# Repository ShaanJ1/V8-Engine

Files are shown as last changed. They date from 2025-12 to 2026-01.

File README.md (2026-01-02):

# V8 Engine
A working 3D printed V8 engine powered by a DC motor with controllable speeds up to 1000RPM.

### Note:
Make sure to lubricate all moving parts to prevent damage to your 3D print. This project was made assuming that this will be printed in ABS, PETG, or another heat-resistant material. If you are using a material like PLA, note that the friction at high speeds may cause the print to very quicky melt, warp, or damage itself in another way.

### Showcase
*Coming soon...*

# Bill of Materials (BOM)

| **Item Name** | **URL** | **Price** | **Quantity** | **Use** |
| --- | --- | ---: | ---: | --- |
| 3D Printing Filament | [Amazon](https://www.amazon.ca/dp/B09DKMW78Y) | $105.06 | 3 x 1KG | 3D filament used (ABS) |
| 12V Battery | [Amazon](https://a.co/d/iR5ZKYJ) | $33.38 | 1 | Power Source |
| DC Motor | [AliExpress](https://www.aliexpress.com/item/1005008221484428.html) | $17.89 | 1 | Spinning Engine |
| Silicone Grease | [AliExpress](https://www.aliexpress.com/item/1005008374157659.html) | $3.65 | 1 | Lubricant for moving parts |
| Heat Shrink | [AliExpress](https://www.aliexpress.com/item/1005008146302901.html) | $3.62 | 1 | For exposed soldered wires |
| PCB | [JLCPCB](https://jlcpcb.com/) | $4.78 | 1 | Main Controller |
| M3 10mm Set Screws | [AliExpress](https://www.aliexpress.com/item/4001081433504.html) | $2.79 | 1 | Main Assembly + Flywheel Screws |
| M4 6mm Screws | [AliExpress](https://www.aliexpress.com/item/1005001785690381.html) | $2.76 | 1 | Motor Mounting Screws |
| M4 16mm Set Screws | [AliExpress](https://www.aliexpress.com/item/1005008512534705.html) | $4.69 | 1 | Connecting Rod Screws |
| M8 25mm Screws | [AliExpress](https://www.aliexpress.com/item/1005006090579821.html) | $4.07 | 1 | Output Gear Holder |
| 5x8 Shaft Coupler | [AliExpress](https://www.aliexpress.com/item/1005006305848755.html) | $6.91 | 1 | Motor to Gear Coupler |
| 608ZZ Bearing | [AliExpress](https://www.aliexpress.com/item/1005010525419357.html) | $4.35 | 1 | Spins output gear |
| 18 AWG Wires (2 ft) | [DigiKey](https://www.digikey.ca/en/products/detail/te-connectivity-aerospace-defense-and-marine/FLHTC0311-18-0/6061732)  | $4.00 | 2 ft | Wiring |
| 100µF Electrolytic Capacitor | [DigiKey](https://www.digikey.ca/en/products/detail/w%C3%BCrth-elektronik/860020473008/5727062) | $0.19 | 1 | Decoupling |
| 0.1µF 0805 Ceramic Capacitor | [DigiKey](https://www.digikey.ca/en/products/detail/kemet/C0805F104K1RACAUTO/26735352) | $0.33 | 1 | Decoupling |
| MBR2045CT | [DigiKey](https://www.digikey.ca/en/products/detail/smc-diode-solutions/MBR2045CT/6022134) | $1.97 | 1 | Motor Flywheeling Diode |
| SS14 | [DigiKey](https://www.digikey.ca/en/products/detail/taiwan-semiconductor-corporation/SS14/7369347) | $0.68 | 2 | Diodes |
| Green LED | [DigiKey](https://www.digikey.ca/en/products/detail/w-rth-elektronik/151051VS04000/4490015) | $0.38 | 1 | ON LED |
| 1206 Fuse 7A 32V | [DigiKey](https://www.digikey.ca/en/products/detail/schurter-inc/3413-0326-22/2644167) | $2.34 | 3 | Circuit Protection |
| 1x2 Terminal Block | [DigiKey](https://www.digikey.ca/en/products/detail/te-connectivity-amp-connectors/282837-2/2187973) | $2.20 | 2 | Power Input, Motor Power |
| IRFZ44 | [DigiKey](https://www.digikey.ca/en/products/detail/infineon-technologies/IRFZ44NPBF/811772) | $2.10 | 1 | N Channel MOSFET |
| MMBT2222A | [DigiKey](https://www.digikey.ca/en/products/detail/shenzhen-slkormicro-semicon-co-ltd/MMBT2222A/25880370) | $0.30 | 2 | NPN transistor |
| IRF9540N | [DigiKey](https://www.digikey.ca/en/products/detail/infineon-technologies/IRF9540NPBF/812088) | $2.89 | 1 | P Channel MOSFET |
| 1K 0402 Resistor | [DigiKey](https://www.digikey.ca/en/products/detail/panasonic-electronic-components/ERJ-2RKF1001X/79729) | $0.44 | 10 | Resistors |
| 1K 0603 Resistor | [DigiKey](https://www.digikey.ca/en/products/detail/stackpole-electronics-inc/RMCF0603FT1K00/1761077) | $0.11 | 10 | Resistors |
| 4.7K 0402 Resistor | [DigiKey](https://www.digikey.ca/en/products/detail/yageo/RC0402FR-074K7L/2827563) | $0.16 | 10 | LED Resistors |
| 10K 0402 Resistor | [DigiKey](https://www.digikey.ca/en/products/detail/yageo/RC0402JR-0710KL/726418) | $0.10 | 10 | Resistors |
| 10K 0603 Resistor | [DigiKey](https://www.digikey.ca/en/products/detail/yageo/RC0603FR-0710KL/726880) | $0.10 | 10 | Resistors |
| NE555P | [DigiKey](https://www.digikey.ca/en/products/detail/texas-instruments/NE555P/277057) | $0.81 | 1 | 555 Timer for PWM |
| AOD4185 | [DigiKey](https://www.digikey.ca/en/products/detail/alpha-omega-semiconductor-inc/AOD4185/2353887) | $1.82 | 1 | Circuit Protection |
| 0805 LED | [DigiKey](https://www.digikey.ca/en/products/detail/w%C3%BCrth-elektronik/150080GS75000/4489915) | $0.30 | 1 | Onboard LED |
| 10K Potentiometer | [DigiKey](https://www.digikey.ca/en/products/detail/bourns-inc/PDB181-K425K-103B/3820304) | $1.94 | 1 | Speed Adjuster |
| PushButton | [DigiKey](https://www.digikey.ca/en/products/detail/same-sky-formerly-cui-devices-/TS02-66-55-BK-160-LCR-D/15634374) | $0.32 | 2 | Start/Stop Buttons |

#### <ins>Totals (not including taxes or shipping)</ins>

**Total (CAD):** $217.43

**Total (USD):** $158.35

### Images
Schematic


PCB


Main Assembly





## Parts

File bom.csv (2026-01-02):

Bill of Materials
Item Name: | URL: | Price: | Quantity: | Use: | Ref (PCB Components): | Spares: (included in quantity)
3D Printing Filament | https://www.amazon.ca/dp/B09DKMW78Y | $105.06 | 3x1KG | 3D filament used (ABS)
12V Battery | https://a.co/d/iR5ZKYJ | $33.38 | 1 | Power Source
DC Motor | https://www.aliexpress.com/item/1005008221484428.html | $17.89 | 1 | Spinning Engine
Silicone Grease | https://www.aliexpress.com/item/1005008374157659.html | $3.65 | 1 | Lubricant for moving parts
Heat Shrink | https://www.aliexpress.com/item/1005008146302901.html | $3.62 | 1 | For exposed soldered wires
3D Print (Shipping) |  | $10.00 | 1 | 3D Print Shipping Costs
PCB | https://jlcpcb.com/ | $4.78 | 1 | Main Controller
M3 10mm Set Screws | https://www.aliexpress.com/item/4001081433504.html | $2.79 | 1 | Main Assembly + Flywheel Screws
M4 6mm Screws | https://www.aliexpress.com/item/1005001785690381.html | $2.76 | 1 | Motor Mounting Screws
M4 16mm Set Screws | https://www.aliexpress.com/item/1005008512534705.html | $4.69 | 1 | Connecting Rod Screws
M8 25mm Screws | https://www.aliexpress.com/item/1005006090579821.html | $4.07 | 1 | Output Gear Holder
5x8 Shaft Coupler | https://www.aliexpress.com/item/1005006305848755.html | $6.91 | 1 | Motor to Gear Coupler
608ZZ Bearing | https://www.aliexpress.com/item/1005010525419357.html | $4.35 | 1 | Spins output gear
18 AWG Wires | https://www.digikey.ca/en/products/detail/te-connectivity-aerospace-defense-and-marine/FLHTC0311-18-0/6061732 | $4.00 | 2ft
100uF Electrolytic Capacitor | https://www.digikey.ca/en/products/detail/w%C3%BCrth-elektronik/860020473008/5727062 | $0.19 | 1 |  | C1
0.1uF 0805 Ceramic Capacitor | https://www.digikey.ca/en/products/detail/kemet/C0805F104K1RACAUTO/26735352 | $0.33 | 1 |  | C4
MBR2045CT | https://www.digikey.ca/en/products/detail/smc-diode-solutions/MBR2045CT/6022134 | $1.97 | 1 |  | D1
SS14 | https://www.digikey.ca/en/products/detail/taiwan-semiconductor-corporation/SS14/7369347 | $0.68 | 2 |  | D2,D3
Green LED | https://www.digikey.ca/en/products/detail/w-rth-elektronik/151051VS04000/4490015 | $0.38 | 1 | ON LED | J6,J9
1206 Fuse 7A 32V | https://www.digikey.ca/en/products/detail/schurter-inc/3413-0326-22/2644167 | $2.34 | 3 |  | F1 | 2
1x2 Terminal Block | https://www.digikey.ca/en/products/detail/te-connectivity-amp-connectors/282837-2/2187973 | $2.20 | 2 | Power Input, Motor Power | J2,J3
IRFZ44 | https://www.digikey.ca/en/products/detail/infineon-technologies/IRFZ44NPBF/811772 | $2.10 | 1 |  | Q1
MMBT2222A | https://www.digikey.ca/en/products/detail/shenzhen-slkormicro-semicon-co-ltd/MMBT2222A/25880370 | $0.30 | 2 |  | Q2,Q5
IRF9540N | https://www.digikey.ca/en/products/detail/infineon-technologies/IRF9540NPBF/812088 | $2.89 | 1 |  | Q4
1K 0402 Resistor | https://www.digikey.ca/en/products/detail/panasonic-electronic-components/ERJ-2RKF1001X/79729 | $0.44 | 10 |  | R1,R2,R5,R7
1K 0603 Resistor | https://www.digikey.ca/en/products/detail/stackpole-electronics-inc/RMCF0603FT1K00/1761077 | $0.11 | 10 |  | R4
4.7K 0402 Resistor | https://www.digikey.ca/en/products/detail/yageo/RC0402FR-074K7L/2827563 | $0.16 | 10 | LED Resistors | R3,R10
10K 0402 Resistor | https://www.digikey.ca/en/products/detail/yageo/RC0402JR-0710KL/726418 | $0.10 | 10 |  | R6,R8,R11
10K 0603 Resistor | https://www.digikey.ca/en/products/detail/yageo/RC0603FR-0710KL/726880 | $0.10 | 10 |  | R12
NE555P | https://www.digikey.ca/en/products/detail/texas-instruments/NE555P/277057 | $0.81 | 1 |  | U1
AOD4185 | https://www.digikey.ca/en/products/detail/alpha-omega-semiconductor-inc/AOD4185/2353887 | $1.82 | 1 |  | Q3
0805 LED | https://www.digikey.ca/en/products/detail/w%C3%BCrth-elektronik/150080GS75000/4489915 | $0.30 | 1 | Onboard LED | D4
10K Potentiometer | https://www.digikey.ca/en/products/detail/bourns-inc/PDB181-K425K-103B/3820304 | $1.94 | 1 | Speed Adjuster
PushButton | https://www.digikey.ca/en/products/detail/same-sky-formerly-cui-devices-/TS02-66-55-BK-160-LCR-D/15634374 | $0.32 | 2 | Start/Stop Buttons
DigiKey Shipping + GST |  | $9.57
 | Total (CAD): | $237.00
 | Total (USD): | $172.60

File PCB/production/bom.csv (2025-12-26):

Designator | Footprint | Quantity | Value | LCSC Part #
C1 | C_Radial_D6.3mm_H11.0mm_P2.50mm | 1 | 100uF
C4 | 0805 | 1 | 100nF
D1 | TO-220-3_Vertical | 1 | MBR2045CT
D2, D3 | D_SMA_Handsoldering | 2 | SS14
D4 | 0805 | 1 | LED
F1 | 1206 | 1 | Fuse
J1, J10, J11, J12, J13, J14, J5, J6, J9 | SolderWire-0.5sqmm_1x01_D0.9mm_OD2.1mm | 9 | Conn_01x01
J2, J3 | TerminalBlock_Phoenix_MKDS-1,5-2-5.08_1x02_P5.08mm_Horizontal | 2 | Screw_Terminal_01x02
Q1 | TO-220-3_Vertical | 1 | Q_NMOS_GDS
Q2, Q5 | SOT-23 | 2 | MMBT2222A
Q3 | TO-252-2 | 1 | Q_PMOS_GDS
Q4 | TO-220-3_Vertical | 1 | IRF9540N
R1, R2, R5, R7 | 0402 | 4 | 1K
R10, R3 | 0402 | 2 | 4.7k
R11, R6, R8 | 0402 | 3 | 10K
R12 | 0603 | 1 | 10K
R4 | 0603 | 1 | 1K
U1 | DIP-8_W7.62mm | 1 | NE555P

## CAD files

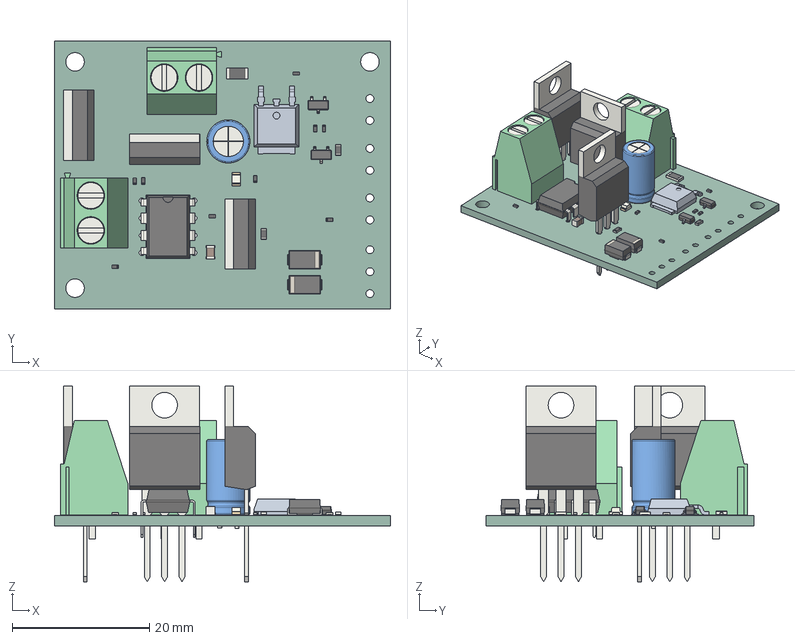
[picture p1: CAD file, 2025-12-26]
CAD/PCB.step
49.0 x 39.1 x 28.5 mm
TO-220-3_Vertical x 3
v8engine 1.2.1
R_0402_1005Metric x 9
SOT-23 x 2
C_Radial_D6.3mm_H11.0mm_P2.50mm
D_SMA x 2
DIP-8_W7.62mm
R_0603_1608Metric x 2
Fuse_1206_3216Metric
TerminalBlock_Phoenix_MKDS-1,5-2-5.08_1x02_P5.08mm_Horizontal x 2
LED_0805_2012Metric
C_0805_2012Metric
v8engine_PCB

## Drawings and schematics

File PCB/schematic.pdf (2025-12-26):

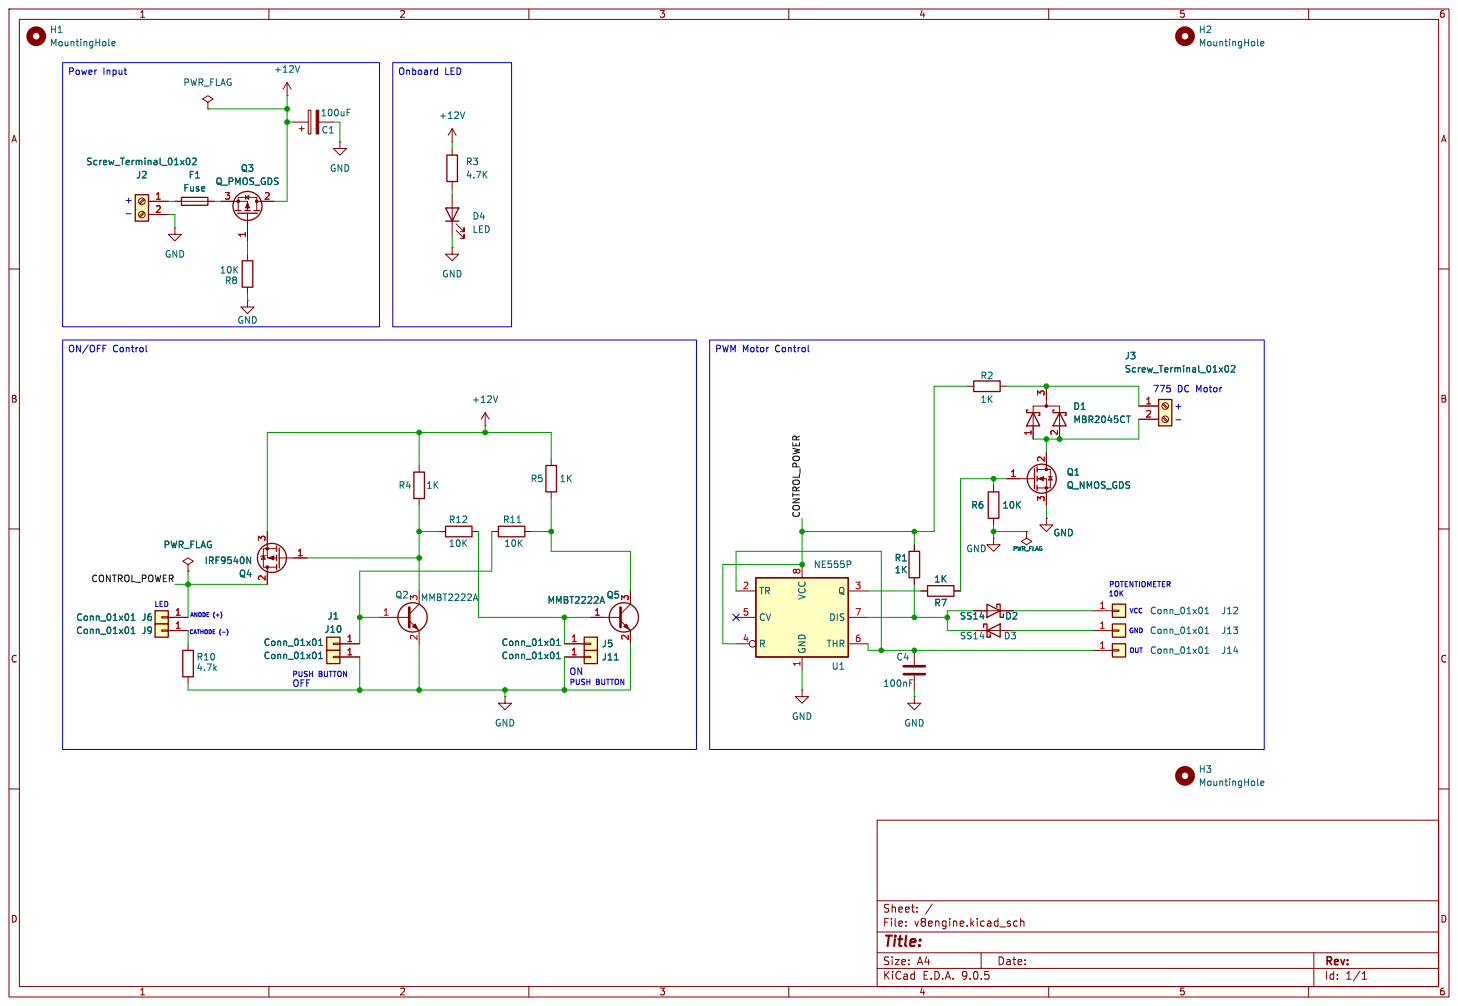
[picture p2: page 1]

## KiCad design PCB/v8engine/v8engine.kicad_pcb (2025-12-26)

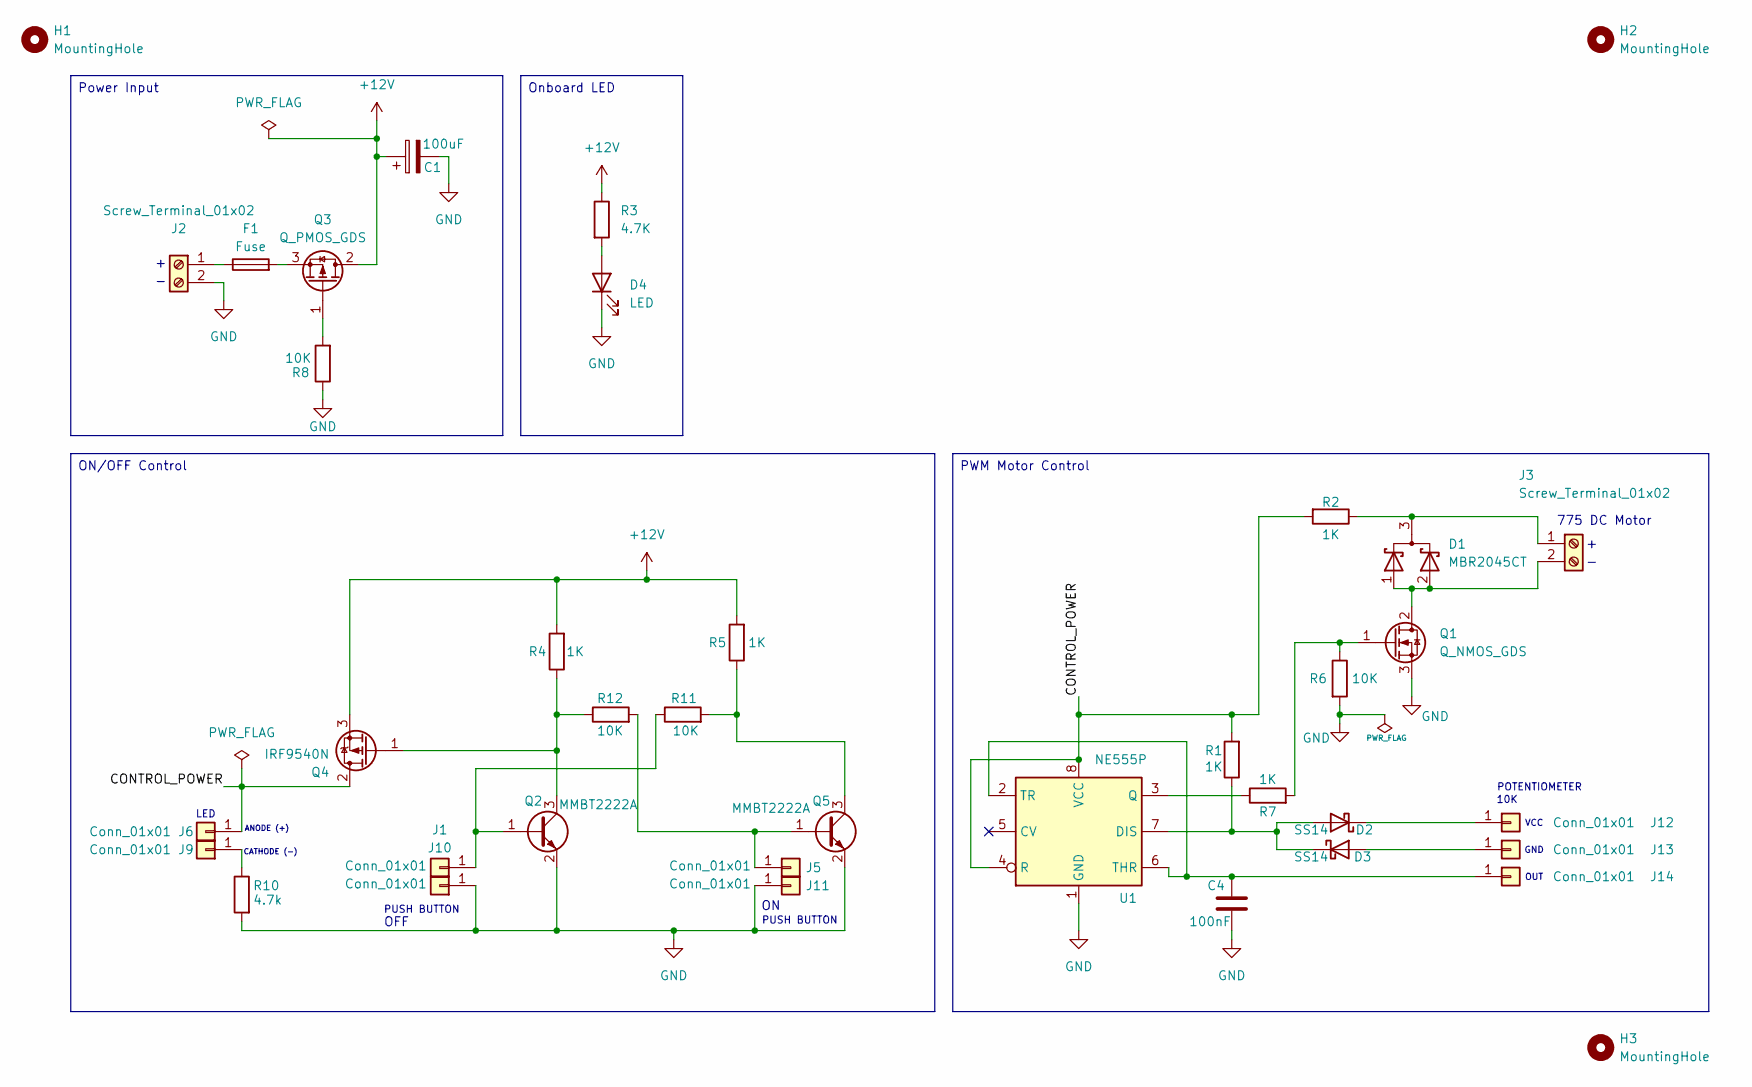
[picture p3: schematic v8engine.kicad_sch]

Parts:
C1: 100uF; C_Radial_D6.3mm_H11.0mm_P2.50mm
C4: 100nF; C_0805_2012Metric_Pad1.18x1.45mm_HandSolder
D1: MBR2045CT; TO-220-3_Vertical
D2, D3: SS14; D_SMA_Handsoldering
D4: LED; LED_0805_2012Metric_Pad1.15x1.40mm_HandSolder
F1: Fuse; Fuse_1206_3216Metric_Pad1.42x1.75mm_HandSolder
H1, H2, H3: MountingHole; MountingHole_2.7mm_M2.5
J1, J5, J6, J9, J10, J11, J12, J13, J14: Conn_01x01; SolderWire-0.5sqmm_1x01_D0.9mm_OD2.1mm
J2, J3: Screw_Terminal_01x02; TerminalBlock_Phoenix_MKDS-1,5-2-5.08_1x02_P5.08mm_Horizont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
Q1: Q_NMOS_GDS; TO-220-3_Vertical
Q2, Q5: MMBT2222A; SOT-23
Q3: Q_PMOS_GDS; TO-252-2
Q4: IRF9540N; TO-220-3_Vertical
R1, R2, R5, R7: 1K; R_0402_1005Metric_Pad0.72x0.64mm_HandSolder
R3: 4.7K; R_0402_1005Metric_Pad0.72x0.64mm_HandSolder
R4: 1K; R_0603_1608Metric_Pad0.98x0.95mm_HandSolder
R6, R8, R11: 10K; R_0402_1005Metric_Pad0.72x0.64mm_HandSolder
R10: 4.7k; R_0402_1005Metric_Pad0.72x0.64mm_HandSolder
R12: 10K; R_0603_1608Metric_Pad0.98x0.95mm_HandSolder
U1: NE555P; DIP-8_W7.62mm

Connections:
+12V: C1.1, Q3.2 (D), Q4.3 (S), R3.1, R4.2, R5.2
/CONTROL_POWER: J6.1, Q4.2 (D), R1.2, R2.2, U1.4 (R), U1.8 (VCC)
GND: C1.2, C4.2, D4.1 (K), J2.2, J10.1, J11.1, Q1.3 (S), Q2.2 (E), Q5.2 (E), R6.2, R8.1, R10.2, U1.1 (GND)
unnamed: D1.3 (K), J3.1, R2.1
unnamed: D2.2 (A), D3.1 (K), R1.1, U1.7 (DIS)
unnamed: D2.1 (K), J12.1
unnamed: D3.2 (A), J13.1
unnamed: D4.2 (A), R3.2
unnamed: J1.1, Q2.1 (B), R11.1
unnamed: F1.1, J2.1
unnamed: D1.1 (A), D1.2 (A), J3.2, Q1.2 (D)
unnamed: J5.1, Q5.1 (B), R12.2
unnamed: J9.1, R10.1
unnamed: C4.1, J14.1, U1.2 (TR), U1.6 (THR)
unnamed: Q1.1 (G), R6.1, R7.2
unnamed: Q2.3 (C), Q4.1 (G), R4.1, R12.1
unnamed: Q3.1 (G), R8.2
unnamed: F1.2, Q3.3 (S)
unnamed: Q5.3 (C), R5.1, R11.2
unnamed: R7.1, U1.3 (Q)

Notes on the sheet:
PUSH BUTTON
LED
775 DC Motor
VCC
GND
OUT
10K
POTENTIOMETER
ANODE (+)
CATHODE (-)
OFF
Onboard LED
PWM Motor Control
ON/OFF Control
Power Input

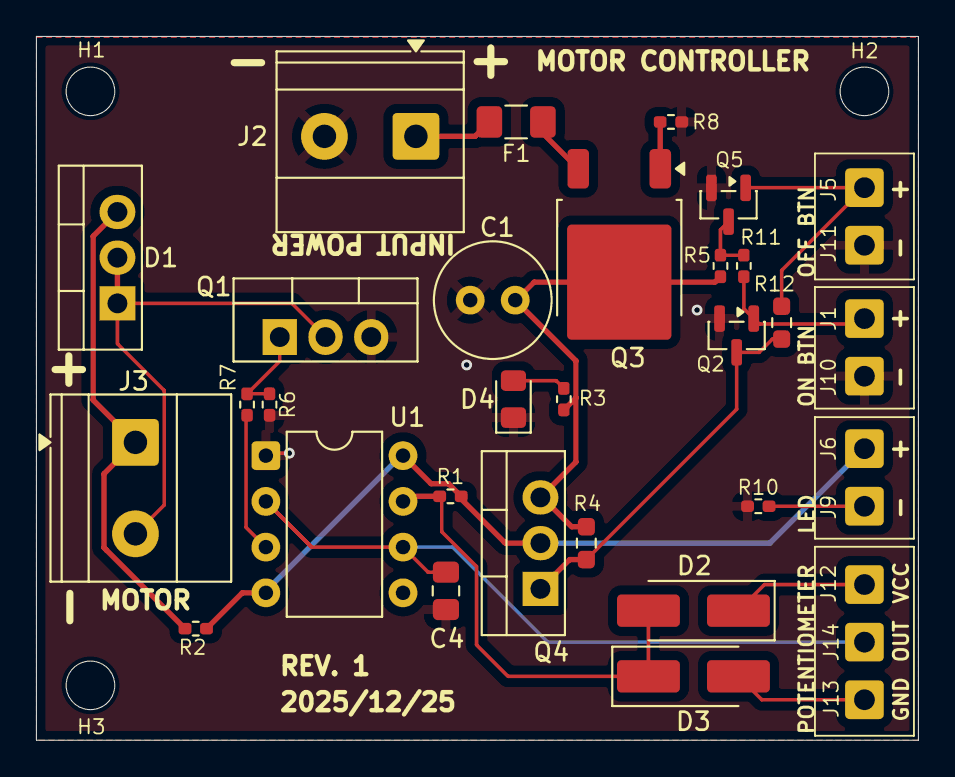
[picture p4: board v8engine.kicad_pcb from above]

Board: 2 copper layers, 49.0 x 39.1 mm, 38 parts (0 on the bottom side), 20 nets.

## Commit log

2025-12-26 update bom
    [bom.csv]
2026-01-01 Adding filament costs
2026-01-02 Added 3D printing filament costs
    [bom.csv]
2026-01-02 update filament costs
    [bom.csv]
